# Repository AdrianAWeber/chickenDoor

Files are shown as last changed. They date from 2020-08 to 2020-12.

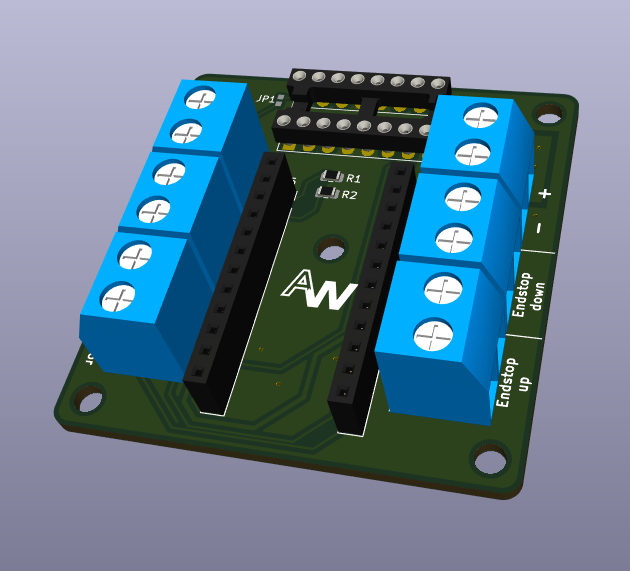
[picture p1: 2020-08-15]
hardware/chickenDoor.png

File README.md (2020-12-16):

# chickenDoor
A Project for a automated chicken door

# Firmware

Clone the Low Power Software from
https://github.com/rocketscream/Low-Power

The .ino file in frirmware is the firmware to be compiled in Arduino IDE. 
It is tested for a Pro Micro 5V/16MHz (Arduino Leonardo)

Already compiled hex file can be found there too.

systemctl stop ModemManager

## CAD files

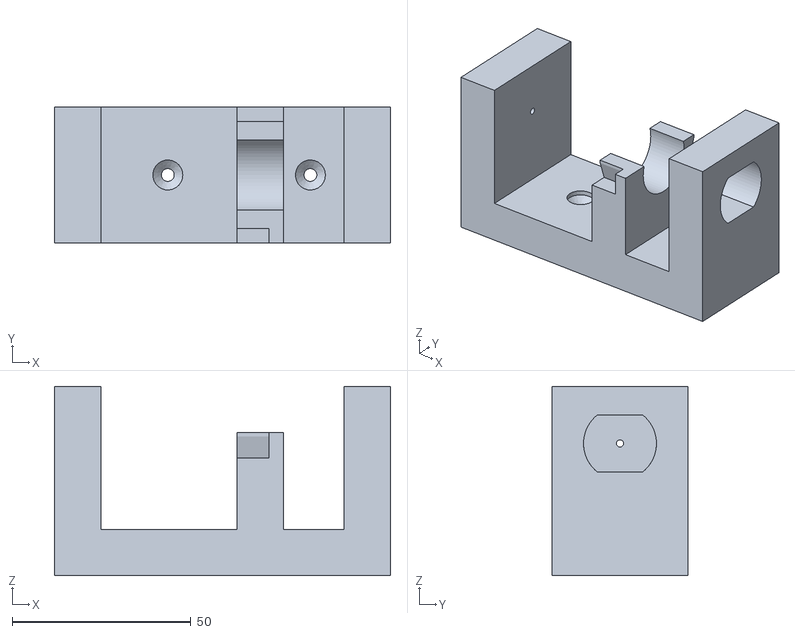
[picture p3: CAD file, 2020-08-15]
3d_print/motorHolder/motorHolder_mainFrame.stl
94.0 x 38.0 x 53.0

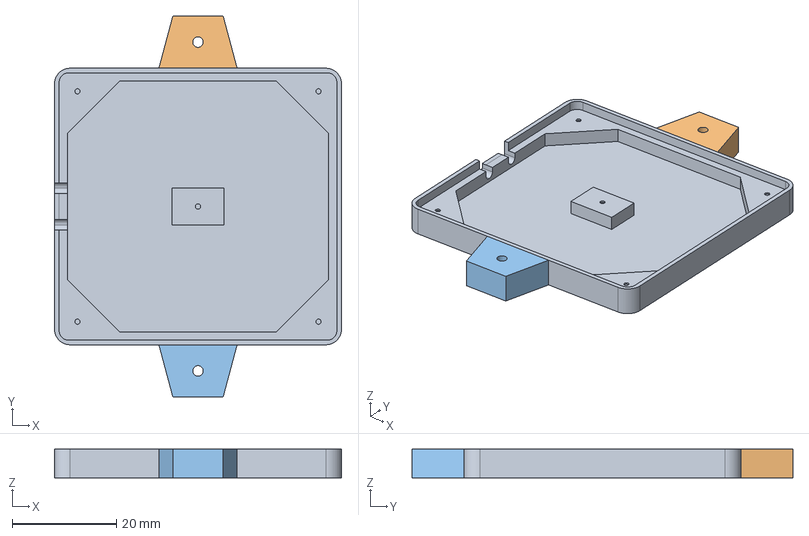
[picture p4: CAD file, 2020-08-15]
3d_print/pcb_holder/chicken_pcb_holder.FCStd
55.0 x 73.0 x 5.50 mm

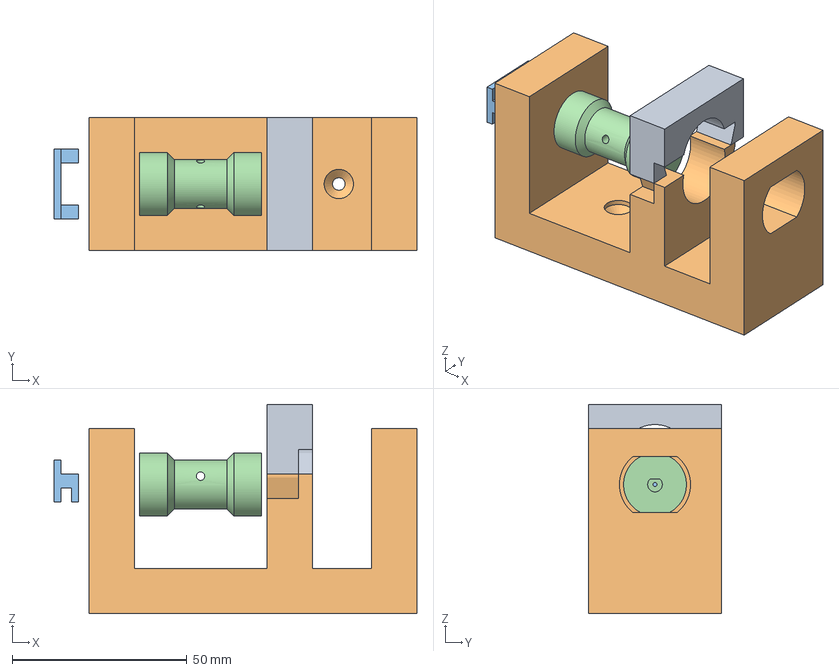
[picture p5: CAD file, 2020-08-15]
3d_print/motorHolder/chicken_motorHolder.FCStd
104.0 x 38.0 x 60.0 mm
Top_Middle
Huhn_v2

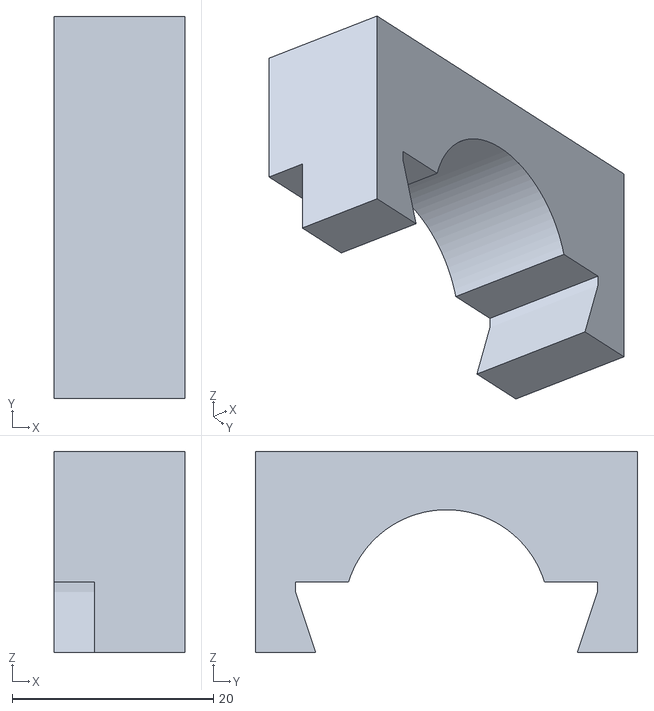
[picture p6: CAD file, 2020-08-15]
3d_print/motorHolder/motorHolder_topMiddelHolder.stl
13.0 x 38.0 x 20.0

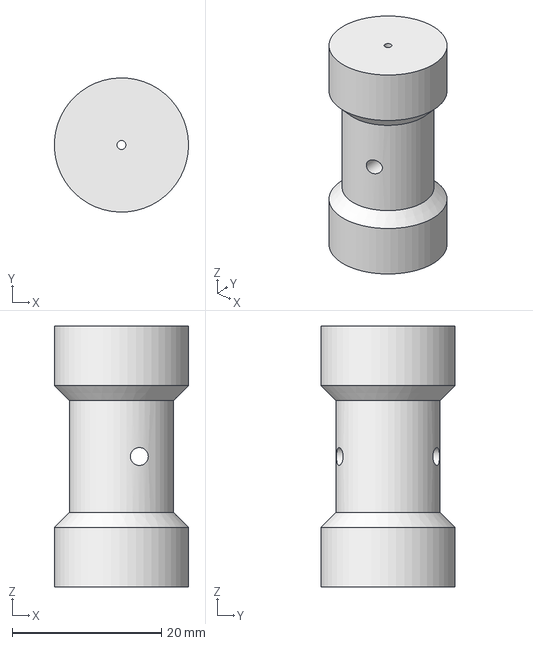
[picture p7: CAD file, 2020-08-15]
3d_print/motorHolder/motor_Axis.FCStd
18.0 x 18.0 x 35.0 mm

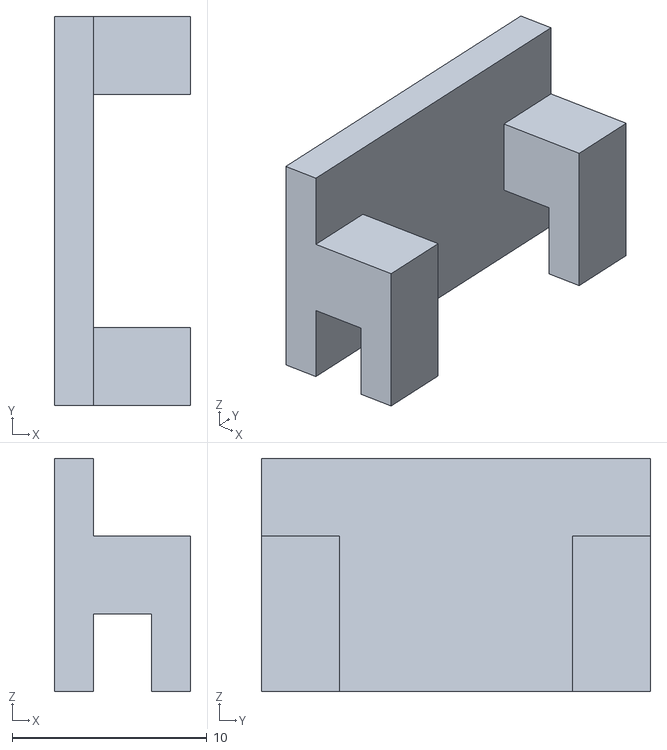
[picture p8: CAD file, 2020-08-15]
3d_print/motorHolder/motorHolder_FrontStopper.stl
7.00 x 20.0 x 12.0

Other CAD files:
3d_print/motorHolder/motor_Axis.stl
3d_print/pcb_holder/chicken_pcb_holder.stl

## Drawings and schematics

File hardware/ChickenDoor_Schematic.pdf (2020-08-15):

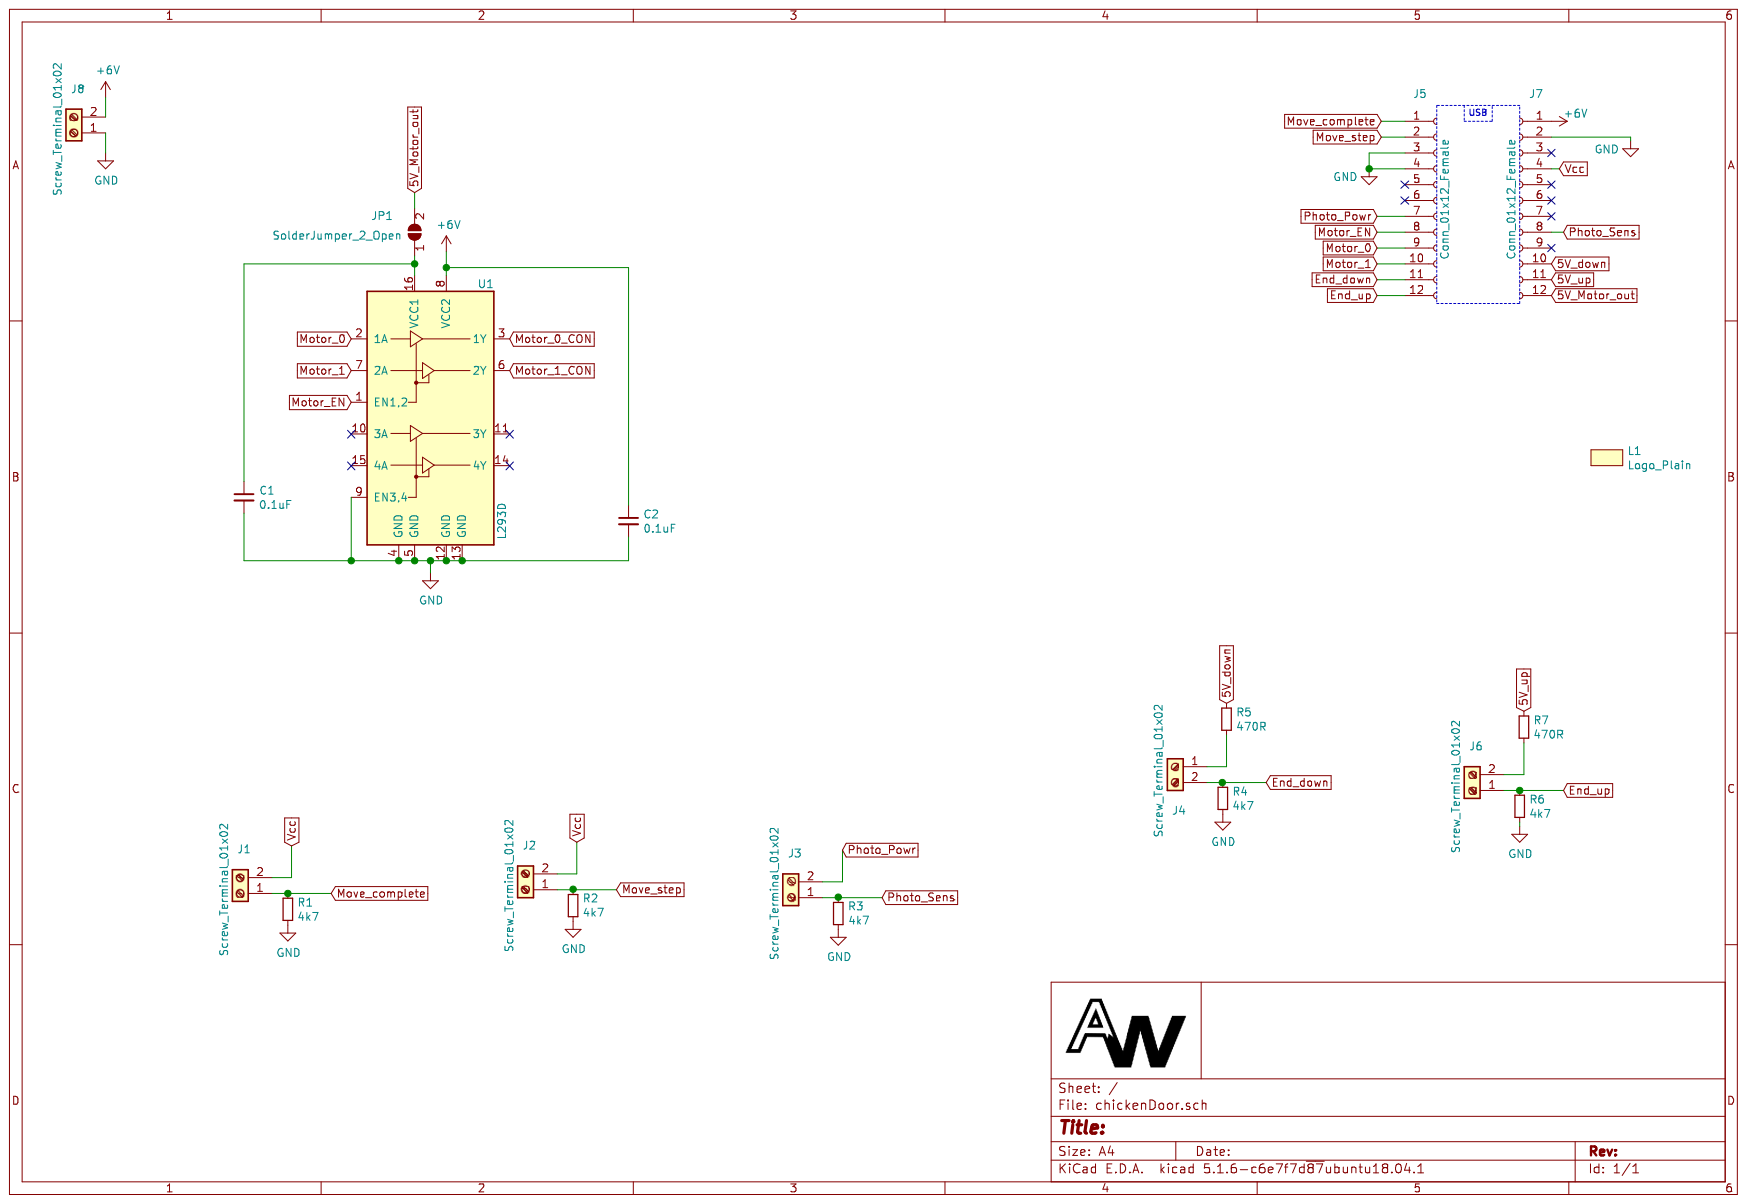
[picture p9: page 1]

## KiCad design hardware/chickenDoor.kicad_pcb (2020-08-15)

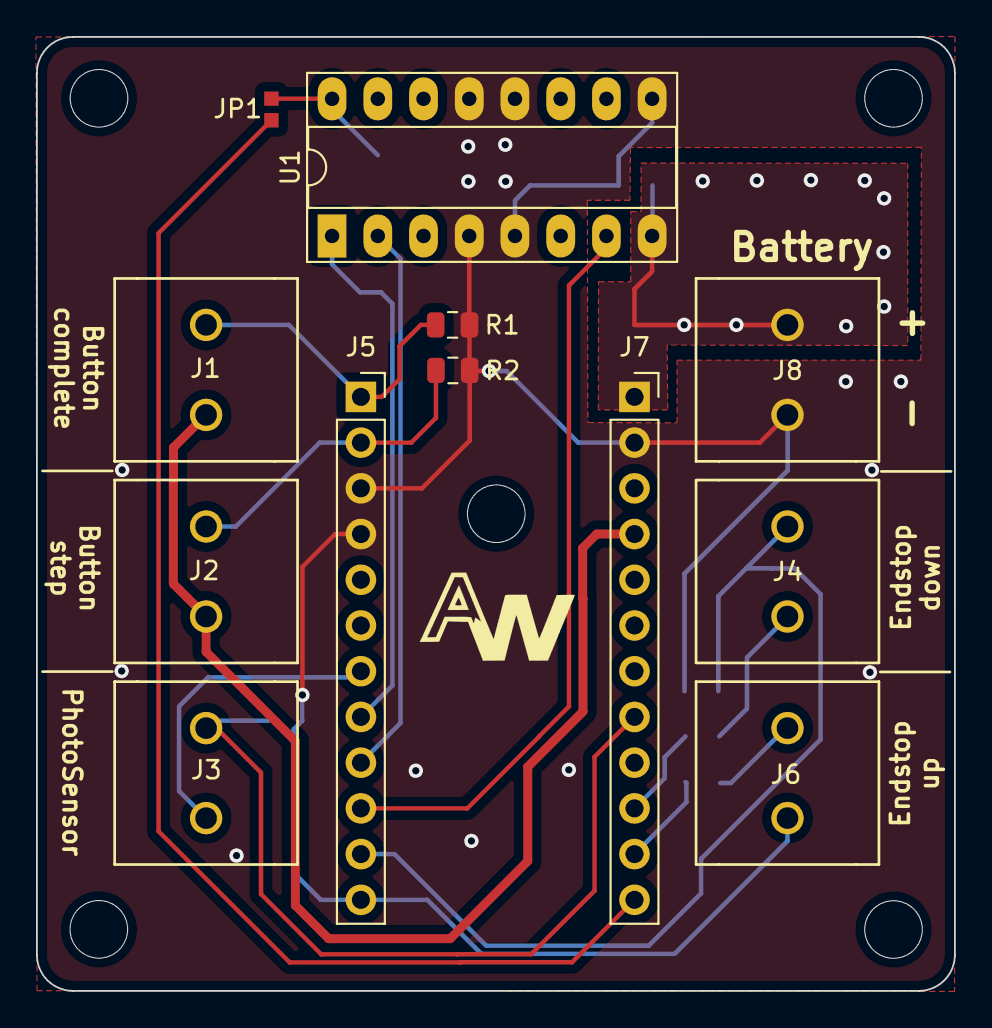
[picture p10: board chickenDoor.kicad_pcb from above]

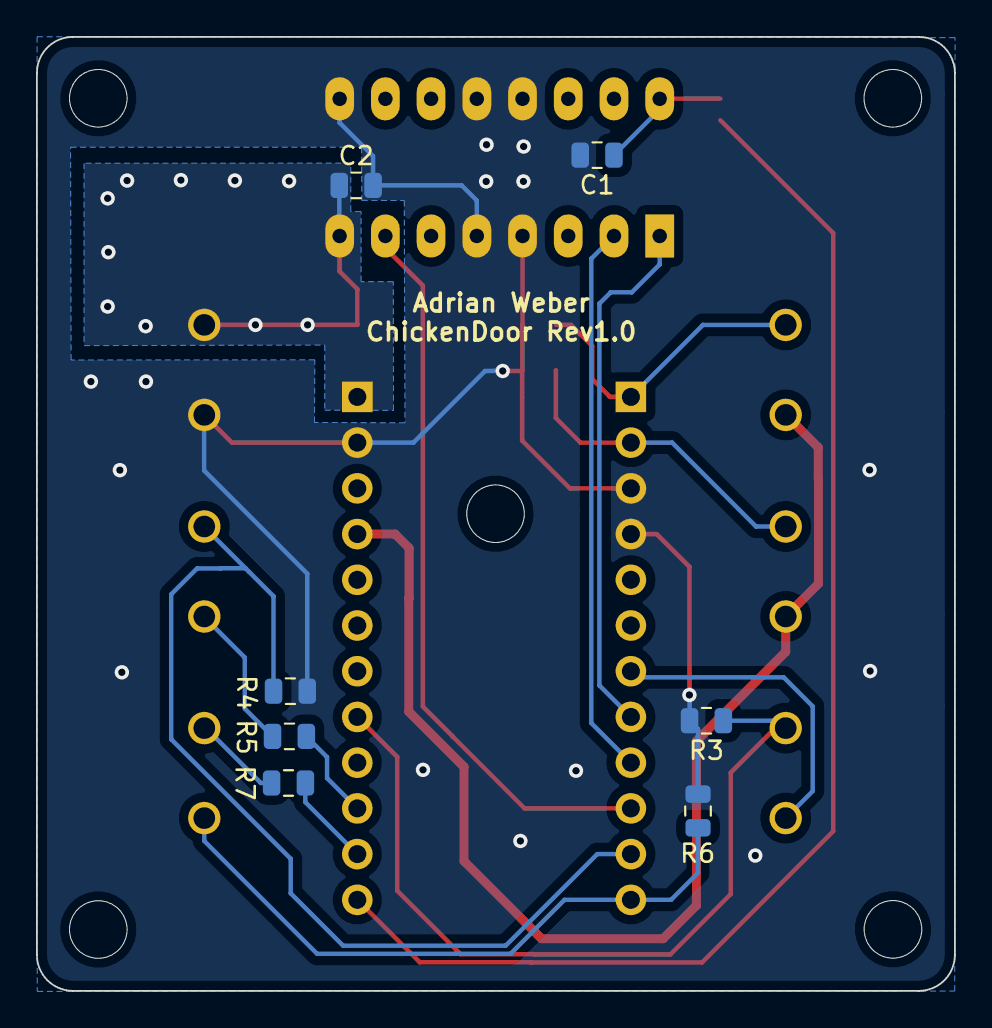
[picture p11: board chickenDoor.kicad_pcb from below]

Board: 2 copper layers, 51.0 x 53.0 mm, 20 parts (7 on the bottom side), 18 nets.

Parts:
C1, C2: 0.1uF; C_0805_2012Metric
J1, J2, J3, J4, J6, J8: Screw_Terminal_01x02; screwterminal
J5, J7: Conn_01x12_Female; PinSocket_1x12_P2.54mm_Vertical
JP1: SolderJumper_2_Open; 2pin
L1: Logo_Plain; Logo_8x5
R1, R2, R3, R4, R6: 4k7; R_0805_2012Metric
R5, R7: 470R; R_0805_2012Metric
U1: L293D; DIP-16_W7.62mm_Socket_LongPads

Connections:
5V_Motor_out: J7.12, JP1.2
5V_down: J7.10, R5.1
5V_up: J7.11, R7.1
+6V: C2.1, J7.1, J8.2, U1.8
End_down: J4.2, J5.11, R4.1
End_up: J5.12, J6.1, R6.1
GND: C1.2, C2.2, J5.3, J5.4, J7.2, J8.1, R1.2, R2.2, R3.2, R4.2, R6.2, U1.4, U1.5, U1.9, U1.12, U1.13
Motor_0: J5.9, U1.2
Motor_1: J5.10, U1.7
Motor_EN: J5.8, U1.1
Move_complete: J1.1, J5.1, R1.1
Move_step: J2.1, J5.2, R2.1
unnamed: C1.1, JP1.1, U1.16
unnamed: J4.1, R5.2
unnamed: J6.2, R7.2
Photo_Powr: J3.2, J5.7
Photo_Sens: J3.1, J7.8, R3.1
Vcc: J1.2, J2.2, J7.4

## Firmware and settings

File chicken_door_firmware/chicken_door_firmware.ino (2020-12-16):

/*
 * CHICKEN DOOR AUTOMATISATION
 * 
 *  Pin 0 -> Interrupt Button_complete
 *  Pin 1 -> Interrupt Buttpn_steps
 *  Pin 2 -> Interrupt DS3231
 *  
 *  Pin 3 -> Switch opened
 *  Pin 4 -> Switch closed
 *  
 *  Pin 5 -> Motor Enable
 *  Pin 6 -> Motor connection A
 *  Pin 7 -> Motor connection B
 */

//TODO: Check if Pin 0 can be used for pin 2; otherwise fix it on PCB
//      PCB has no MOTOR Connector ...

#include <EEPROM.h>
#include <avr/sleep.h>
#include "LowPower.h"

/**
 * Digital Pins
 */
 
#define MOVE_COMPLETE 1
#define MOVE_STEP 0
#define BTN_step_read 2
#define Photo_Pwr 4
#define Motor_En 5
#define Motor_B 6
#define Motor_A 7
#define End_down 8
#define End_up 9
#define DOWN_5V 14
#define UP_5V   16
#define MOTOR_OUT_5V 10

/**
 * Analog Pins
 */
#define PR 0 // analog Pin0  -> A0 | PhotoSensor Measurement


#define TIME_OPEN  17000
#define TIME_CLOSE 11200

#define LightThreshold_close 18
#define LightThreshold_open 25

byte position_door = 0;
byte dir           = 0;  // 0: down; 1: up
byte pressed       = 0;

byte move_complete_interr = 0;
byte move_step_interr     = 1;

unsigned int light         = 1000;
unsigned int light_pre     = 1000;

//Measure not permamntly: interval can be set here 
unsigned int timecnt       = 0 ; 
unsigned int TimeIntervall = 5;//225; // Multiple of 8 sec   

void setup() {
  // Read position of door  -> Address 0
  position_door = EEPROM.read(0);  // 0 -> closed ; 1-> open
  pinMode(Motor_En, OUTPUT);
  pinMode(Motor_A, OUTPUT);
  pinMode(Motor_B, OUTPUT);
  pinMode(Photo_Pwr, OUTPUT);
  pinMode(DOWN_5V, OUTPUT);
  pinMode(UP_5V, OUTPUT);
  pinMode(MOTOR_OUT_5V, OUTPUT);

  digitalWrite(Motor_En,LOW); // Stop
  digitalWrite(Motor_A,LOW);   // Save power
  digitalWrite(Motor_B,LOW);
  digitalWrite(Photo_Pwr,LOW);
  digitalWrite(DOWN_5V,LOW);
  digitalWrite(UP_5V,LOW);
  digitalWrite(MOTOR_OUT_5V,LOW);
     
  attachInterrupt(digitalPinToInterrupt(MOVE_COMPLETE), move_complete_ISR, RISING);
  attachInterrupt(digitalPinToInterrupt(MOVE_STEP), move_step_ISR, RISING);
  //Serial.begin(9600);
}

void loop() {

//LowPower.idle(SLEEP_8S, ADC_OFF, TIMER4_OFF, TIMER3_OFF, TIMER1_OFF, TIMER0_OFF, SPI_OFF, USART1_OFF, TWI_OFF, USB_OFF);
  LowPower.powerDown(SLEEP_8S, ADC_OFF, BOD_OFF);  
  timecnt++;

  if (move_complete_interr == 1){ // Move by Button: complete move to end
    if (position_door == 1){ // open
      close_door(TIME_CLOSE,1);
    } else {
      open_door(TIME_OPEN,1);
    }
    move_complete_interr = 0;
    move_step_interr = 0;
    if (timecnt >= TimeIntervall) {
     timecnt = 0;
    }
  } else if(move_step_interr == 1) {  // Move by Button: Just as lang as button is holded; Stopped by Reeds

    if (dir == 0){
      down();
      dir = 1;
    } else {
      up();
      dir = 0;
    }
    digitalWrite(Motor_En, HIGH);
    while (move_step_interr == 1) {
      delay(200);
      move_step_interr = digitalRead(MOVE_STEP);//digitalRead(BTN_step_read);
        
      /*if ((move_step_interr == 1)) {
        int endPos = 0;
        if (dir == 1) endPos = digitalRead(End_down); // moving down
        if (dir == 0) endPos = digitalRead(End_up);
        if (endPos == 1) move_step_interr = 0; // break loop due to End of door
      }*/
    }

    // Stop Motor again
    digitalWrite(Motor_En,LOW); // Stop
    digitalWrite(Motor_A,LOW);   // Save power
    digitalWrite(Motor_B,LOW);
    digitalWrite(MOTOR_OUT_5V,LOW);

    //Unpower the Reeds
    //if (STOP_BY_SENSOR == 1) { 
      digitalWrite(DOWN_5V,LOW);
      digitalWrite(UP_5V,LOW);
    //}
     
    move_complete_interr = 0;
    move_step_interr = 0;
    if (timecnt >= TimeIntervall) {
      timecnt = 0;
    }
 
  } else {  //Move by Ligh Sensor
    if (timecnt >= TimeIntervall) {
      digitalWrite(Photo_Pwr,HIGH); delay(100);
      light = analogRead(PR); delay (100);
      digitalWrite(Photo_Pwr,LOW);

      // evening
      if (light <= LightThreshold_close && light_pre > LightThreshold_close && position_door == 1){
        int timeOutVar = close_door(TIME_CLOSE,1);
        if ( timeOutVar > 0) { // first try did not work out.
          close_door_ifTimeout(TIME_CLOSE,0); // close by time. Inverted due to order on line
        }
      } else if (light > LightThreshold_open && light_pre <= LightThreshold_open && position_door == 0) {
         if (open_door(TIME_OPEN,1) == 1){ // Timeout!
           // TODO: Do something in case of timeout
         }
      }
      
      light_pre = light;
     
      move_complete_interr = 0;
      move_step_interr = 0;
      timecnt = 0;
    }
  }
}//loop


// open the door
byte open_door(unsigned int open_time, unsigned int STOP_BY_SENSOR){
  //Motor Settings for upwards
  up();

  byte timeoutFlag = 0;
 
  // enable Motor
  digitalWrite(Motor_En, HIGH);

  if (STOP_BY_SENSOR == 1) {
    bool endPos = 0;
    unsigned int cntTime = 0;
    while (endPos == 0){
      endPos = digitalRead(End_up);
      delay(5); // 5ms;
      cntTime++;
      if (cntTime > 6000) {// ~30 sek; Timeout
        timeoutFlag = 1;
        break; 
      }
    }
  } else { // stop by time
    delay(open_time);
  }
  
  digitalWrite(Motor_En,LOW); // Stop
  digitalWrite(Motor_A,LOW);  // Save power
  digitalWrite(Motor_B,LOW);
  digitalWrite(MOTOR_OUT_5V,LOW);

  //Unpower the Reeds
  //if (STOP_BY_SENSOR == 1) { 
    digitalWrite(DOWN_5V,LOW);
    digitalWrite(UP_5V,LOW);
 // }

  // Save status to EEPROM
  // Even if timeout is active, door is most likely open as no sideflip of string is possible.
  EEPROM.write(0,1); // open
  position_door = 1;

  return timeoutFlag;
}


// close door if Timeout
byte close_door_ifTimeout(unsigned int open_time, unsigned int STOP_BY_SENSOR){
  //Motor Settings for upwards
  up();

  byte timeoutFlag = 0;
 
  // enable Motor
  digitalWrite(Motor_En, HIGH);

  if (STOP_BY_SENSOR == 1) {
    bool endPos = 0;
    unsigned int cntTime = 0;
    while (endPos == 0){
      endPos = digitalRead(End_up);
      delay(5); // 5ms;
      cntTime++;
      if (cntTime > 6000) {// ~30 sek; Timeout
        timeoutFlag = 1;
        break; 
      }
    }
  } else { // stop by time
    delay(open_time);
  }
  
  digitalWrite(Motor_En,LOW); // Stop
  digitalWrite(Motor_A,LOW);  // Save power
  digitalWrite(Motor_B,LOW);
  digitalWrite(MOTOR_OUT_5V,LOW);

  //Unpower the Reeds
  //if (STOP_BY_SENSOR == 1) { 
    digitalWrite(DOWN_5V,LOW);
    digitalWrite(UP_5V,LOW);
 // }

  // Save status to EEPROM
  // Even if timeout is active, door is most likely open as no sideflip of string is possible.
  EEPROM.write(0,0); // close
  position_door = 0;

  return timeoutFlag;
}


//close the door
byte close_door(unsigned int closeTime, unsigned int STOP_BY_SENSOR){
  // Motor Setting to close door
  down();

  byte timeoutFlag = 0;  // O: Closed; 1: opened again; 2: Timeout
  
  // enable Motor
  digitalWrite(Motor_En, HIGH);

  if (STOP_BY_SENSOR == 1) {
    bool endPos = 0;
    unsigned int cntTime = 0;
    while (endPos == 0){
      endPos = digitalRead(End_down);
      if (endPos == 1) {
        timeoutFlag = 0;
        break;
      } else {
        if (cntTime > 600) {  //~ 3sek to avoid measurement in open position.
          endPos = digitalRead(End_up);
          if (endPos == 1) {
            timeoutFlag = 1; // again in opened position;
            endPos = 1;
            break;
          }
        }
      }
      delay(5); // 5ms;
      cntTime++;
      if (cntTime > 6000) {// ~30 sek; Timeout
        timeoutFlag = 2;
        endPos = 1;
        break; 
      }
    }
  } else { // stop by time
    delay(closeTime);
  }
  
  // Stop Motor again
  digitalWrite(Motor_En,LOW); // Stop
  digitalWrite(Motor_A,LOW);  // Save power
  digitalWrite(Motor_B,LOW);
  digitalWrite(MOTOR_OUT_5V,LOW);

  //Unpower the Reeds
  //if (STOP_BY_SENSOR == 1) { 
    digitalWrite(DOWN_5V,LOW);
    digitalWrite(UP_5V,LOW);
  //}  

  // Save status to EEPROM
  if (timeoutFlag == 0) {
    EEPROM.write(0,0); // closed
    position_door = 0;
  } else if (timeoutFlag == 1){
    EEPROM.write(0,1); // open
    position_door = 1;
  } else { // Timeout: we think we are open.
    EEPROM.write(0,1); // open
    position_door = 1;
  }

  return timeoutFlag; 
}

void up(){
  digitalWrite(MOTOR_OUT_5V,HIGH);
   // Motor will turn right
  digitalWrite(Motor_A,HIGH);   
  digitalWrite(Motor_B,LOW);

  //power the upwards Reed 
  //if (STOP_BY_SENSOR == 1) 
  digitalWrite(UP_5V,HIGH);
  digitalWrite(DOWN_5V,HIGH);
}

void down(){
  digitalWrite(MOTOR_OUT_5V,HIGH);
   // Motor will turn left
  digitalWrite(Motor_A,LOW);   
  digitalWrite(Motor_B,HIGH);

  //power the downwards Reed 
  //if (STOP_BY_SENSOR == 1) 
  digitalWrite(DOWN_5V,HIGH);
  digitalWrite(UP_5V,HIGH);
}

void move_complete_ISR(){
  move_complete_interr = 1;
}

void move_step_ISR(){
  move_step_interr = 1;
}

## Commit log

2020-08-15 3d Files for the motor Holder and the PCB Holder
    [chicken_motorHolder.FCStd, chicken_pcb_holder.FCStd, chicken_pcb_holder.stl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]
2020-08-15 PCB files
    [chickenDoor-B_Cu.gbr, chickenDoor-B_Mask.gbr, chickenDoor-B_Paste.gbr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]
2020-10-31 fix: Retry and safety solution for case of a non working stop sensor
    [chicken_door_firmware.ino]
